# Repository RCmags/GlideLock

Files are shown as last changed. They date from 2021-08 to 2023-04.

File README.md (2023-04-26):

# Glide Lock for a radio-controlled ornithopter :bird:
This Arduino sketch is the [glide lock](http://ovirc.free.fr/GLDAB_English.php) for a crank-driven ornithopter. It's meant to stop the wings at a small dihedral angle when the motor is turned off.  

## How it works
The system works by iddling the motor below a certain throttle until the crankshaft reaches a known position. The position of the rotor is measured using a hall sensor and a magnet attached to the crank shaft. When the magnet passes in front of the sensor, the motor turns off. However, the motor will continue to spin even after the throttle is set to zero. To work around this, one can continue to spin the motor for a short time interval after the magnet passes the sensor. If this delay is tuned correctly, the crank will stop in more or less the desired position. 

## Schematics

### Arduino nano: 
The code can accommodate either an analog or digital hall sensor as both use the same circuit.

<p align="center"> 
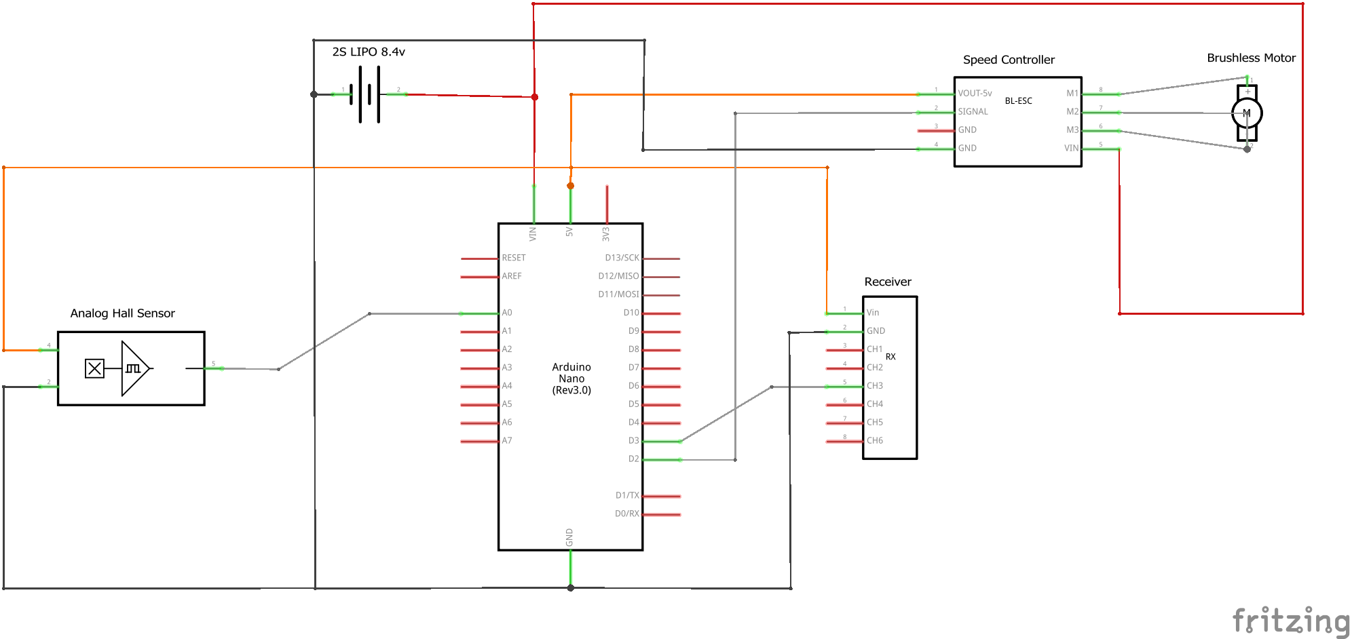
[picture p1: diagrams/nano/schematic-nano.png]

</p>

### DigiSpark ATTiny85: 
Due to some odd behaviour, the input pin for the hall sensor has to change depending on whether it is analog or digital. Use __P0 for digital__  and __P4 for analog__. 
  
<p align="center"> 
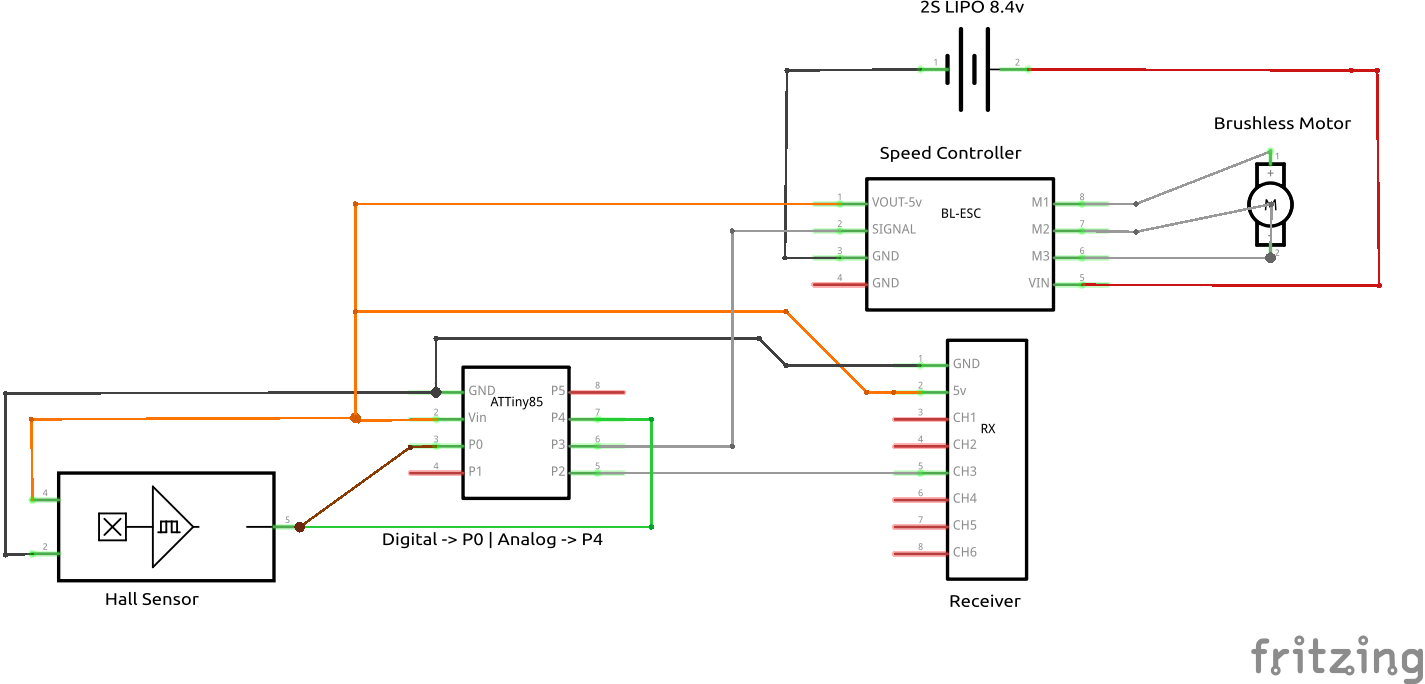
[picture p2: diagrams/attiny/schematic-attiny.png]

</p>

## Dependencies
The ATTiny code requires [ATTinyCore](https://github.com/SpenceKonde/ATTinyCore) to compile. 

## Example
See: [Video explaining the Glide Lock and how it operates](https://youtu.be/v0z1ojpoehQ)

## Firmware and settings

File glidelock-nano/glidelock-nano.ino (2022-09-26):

/* ORNITHOPTER GLIDE LOCK */

/* Sketch for an arduino NANO that controls the motor of an RC ornithopter. 
 * It commands the motor to stop once the crank shaft reaches a hall sensor pickup.
 * Author: RCmags https://github.com/RCmags
*/

//=============== Connections ================
// See included schematic
  // Inputs:
// Pin 3  -> Receiver CH3
// Pin A0 -> Hall sensor
  // Outputs:
// Pin 2  -> Motor ESC 

//=================== Code ===================
#include <Servo.h>
#include "parameters.cpp"

//---- constants
#define SENSOR_PIN      A0    // Must be analog pin if sensor is analog, otherwise use any pin.  
#define INPUT_PIN       3     // Receiver input. Digital pin with interrupt
#define MOTOR_PIN       2     // Output Pin for motor ESC. 

#define NUMBER_MEAN     50    // number of readings used for calibration mean 
#define TIME_CALIBRATE  1000  // timer interval over which readings are averaged [microseconds]

//---- global variables

volatile uint16_t pwm_input = 0;
Servo motor;

//---- PWM input

/* interrupt routine to read pwm pulse */
void checkPwmInput() {
  static uint32_t initial_time = micros();
  if( digitalRead(INPUT_PIN) ) {    // rising 
    initial_time = micros();
  } else {                          // falling
    pwm_input = micros() - initial_time;
  }
}

//---- hall sensor

#ifdef USING_ANALOG_SENSOR

/* average of sensor output */
int calibrateSensor() {
  constexpr int DELAY = int( float(TIME_CALIBRATE)/float(NUMBER_MEAN) );
  float sum = 0;
  for( uint8_t index = 0; index < NUMBER_MEAN; index += 1 ) {
    sum += float( analogRead(SENSOR_PIN) );
    delayMicroseconds(DELAY); 
  } 
  sum /= float(NUMBER_MEAN);
  return int(sum);
}

/* set pin and calibrate sensor */
void setupSensor() {
  pinMode(SENSOR_PIN, INPUT_PULLUP);
  readSensor();                                 // Calibrate with first call
}

/* convert analog reading to digital output */
bool readSensor() {
  static int sensor_mean = calibrateSensor();   // Store mean in local scope
  int input = analogRead(SENSOR_PIN) - sensor_mean;  
  return input > SENSOR_HIGH ? HIGH : LOW;
}

#else // using digital sensor

void setupSensor() {
  pinMode(SENSOR_PIN, INPUT_PULLUP);
}

bool readSensor() {
  return !digitalRead(SENSOR_PIN);
}
#endif

//---- main loop

void setup() {
  // set pins
  setupSensor();
  pinMode(INPUT_PIN, INPUT_PULLUP);  
  pinMode(LED_BUILTIN, OUTPUT);

  // pwm interrupt
  attachInterrupt( digitalPinToInterrupt(INPUT_PIN), checkPwmInput, CHANGE );

  // set throttle to zero
  motor.attach(MOTOR_PIN);
  motor.writeMicroseconds(PWM_MIN);
  delay(DELAY_STARTUP);
  
  // blink led - startup warning
  for( int index = 0; index < 5; index += 1 ) {
    digitalWrite( LED_BUILTIN, HIGH );
    delay(100);
    digitalWrite( LED_BUILTIN, LOW );
    delay(100);
  }
}

void loop() {
  // delay timer
  static uint32_t idle_timer = millis();
  
  // Select mode
  if( pwm_input < PWM_IDLE ) {
    // idle motor
    uint32_t dt = millis() - idle_timer;
    if( dt < DELAY_IDLE ) {
      motor.writeMicroseconds(PWM_IDLE);
    } else {
      // stop crank above sensor
      if( readSensor() ) {  
        delay(DELAY_POSITION);
        motor.writeMicroseconds(PWM_MIN);
      }
    }     
  // throttle beyond cutoff
  } else { 
    motor.writeMicroseconds(pwm_input);
    idle_timer = millis();
  }
}

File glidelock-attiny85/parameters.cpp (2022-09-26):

/*      CONSTANT     |    VALUE   |  UNIT  |   DESCRIPTION */
/*=========================================================*/
// 1. Delays
#define DELAY_STARTUP     8000    // ms     // Delay to arm ESC. Must be large enough to ensure startup. 
#define DELAY_IDLE        800     // ms     // Delay to allow motor to slow down to idle speed. Must be large enough to ensure decceleration.
#define DELAY_POSITION    40      // ms     // Delay to offset crank relative to sensor. A larger value causes a larger overshoot. 

// 2. PWM signal 
#define PWM_IDLE          1250    // us     // Throttle when iddling to find sensor. A larger values causes the crank to overshoot the sensor.
#define PWM_MIN           1050    // us     // Zero throttle. If using a BLheli esc, PWM_MIN < BLHELI_PWM_MIN  

// 3. Input deadband filter
#define INPUT_CHANGE      12      // us     // Change in PWM signal needed to update receiver inputs

// 4. Hall sensor
//#define USING_ANALOG_SENSOR                 // remove comment if using an analog hall sensor                                  
#define SENSOR_HIGH       100               // Values above threshold are high. Reading is relative to mean sensor output.   

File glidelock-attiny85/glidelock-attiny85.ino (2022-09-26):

/* ORNITHOPTER GLIDE LOCK */

/* Sketch for an ATTiny85 that controls the motor of an RC ornithopter. 
 * It commands the motor to stop once the crank shaft reaches a hall sensor pickup.
 * Author: RCmags https://github.com/RCmags
 * 
 * NOTE: Code is intended to be used with ATTinyCore
*/

//=============== Connections ================
// See included schematic
  // Inputs:
// Pin 2 -> Receiver CH3
// The sensor pin depends on the type of sensor:
/* Pin 4 -> Analog Hall sensor 
 * Pin 0 -> Digital Hall sensor */
  // Outputs:
// Pin 3 -> Motor ESC 

//=================== Code ===================
#include <Servo_ATTinyCore.h>
#include "parameters.cpp"

//---- constants
#define NUMBER_MEAN     50    // number of readings used for calibration mean 
#define TIME_CALIBRATE  1000  // timer interval over which readings are averaged [microseconds]

//---- global variables

volatile uint16_t pwm_input = 0;
Servo motor;

//----- Input signal
// PORTB = {0 .. 5} -> using pin {2} = B00000100

/* port change interrupt to read PWM input from receiver */
ISR( PCINT0_vect ) {
  static uint32_t initial_time = 0; 
  static uint8_t port_last = PINB;  
  
  // port changes
  uint32_t current_time = micros(); 
  uint8_t port_rise = ~port_last & PINB;
  uint8_t port_fall = port_last & ~PINB;
  
  // check changing pin
  constexpr uint8_t mask = 1 << PCINT2; 
  if( port_rise & mask ) {                
      initial_time = current_time;
  } else if ( port_fall & mask ) {       
      pwm_input = current_time - initial_time;
  }
  port_last = PINB;    
}

void setupISR() {
  // enable pin change interrupts
  GIMSK |= (1 << PCIE);     
  // set pin as PCINT
  PCMSK |= (1 << PCINT2);   
  // set as input
  pinMode(PB2, INPUT_PULLUP);    
}

//---- input filter

/* apply deadband to pwm signal to reduce noise */
int filterInput() {
  static int last_input = 0;
  int change = int(pwm_input) - last_input;
  last_input = change >  INPUT_CHANGE ? pwm_input - INPUT_CHANGE :
               change < -INPUT_CHANGE ? pwm_input + INPUT_CHANGE : last_input;
  return last_input;
}

//---- hall sensor

#ifdef USING_ANALOG_SENSOR

  // Pin mapping: PB4 -> Analog 2 
#define ANALOG_PIN    2

/* average of sensor output */
int calibrateSensor() {
  constexpr int DELAY = int( float(TIME_CALIBRATE)/float(NUMBER_MEAN) );
  float sum = 0;
  for( uint8_t index = 0; index < NUMBER_MEAN; index += 1 ) {
    sum += float( analogRead(ANALOG_PIN) );
    delayMicroseconds(DELAY); 
  } 
  sum /= float(NUMBER_MEAN);
  return int(sum);
}

/* set pin and calibrate sensor */
void setupSensor() {
  pinMode(PB4, INPUT_PULLUP);
  readSensor();                                 // Calibrate with first call
}

/* convert analog reading to digital output */
bool readSensor() {
  static int sensor_mean = calibrateSensor();   // Store mean in local scope
  int input = analogRead(ANALOG_PIN) - sensor_mean;      
  return input > SENSOR_HIGH ? HIGH : LOW;
}

#else // Digital sensor. Uses different pin for stability

bool readSensor() {
  return !digitalRead(PB0);
}

void setupSensor() {
  pinMode(PB0, INPUT_PULLUP);  
}
#endif

//---- main loop

void setup() {
  // set pins
  setupISR();             // rx signal
  setupSensor();          // sensor
  pinMode(PB3, OUTPUT);   // motor
  pinMode(LED_BUILTIN, OUTPUT);

  // set throttle to zero
  motor.attach(PB3);
  motor.writeMicroseconds(PWM_MIN);
  delay(DELAY_STARTUP);
  
  // blink led - startup warning
  for( int index = 0; index < 5; index += 1 ) {
    digitalWrite( LED_BUILTIN, HIGH );
    delay(100);
    digitalWrite( LED_BUILTIN, LOW );
    delay(100);
  }
}

void loop() {  
  // delay timer
  static uint32_t idle_timer = millis();
  
  // Select mode
  int input = filterInput();
  
  if( input < PWM_IDLE ) {
    // idle motor
    uint32_t dt = millis() - idle_timer;
    if( dt < DELAY_IDLE ) {
      motor.writeMicroseconds(PWM_IDLE);
    } else {
      // stop crank above sensor
      if( readSensor() ) {  
        delay(DELAY_POSITION);
        motor.writeMicroseconds(PWM_MIN);
      }
    }     
  // throttle beyond cutoff
  } else { 
    motor.writeMicroseconds(input);
    idle_timer = millis();
  }
}

// Note: Not all pin selections result in the desired output, hence the pin switching.

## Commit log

2021-08-23 first version of lock
    includes version for analog and digital hall effect sensors.
2021-08-25 analog schematic
2021-08-25 added schematic
2022-08-11 dual sensor type
2023-04-24 added fritzing diagrams
    [glide-lock-attiny.fzz, glide-lock-nano.fzz]
